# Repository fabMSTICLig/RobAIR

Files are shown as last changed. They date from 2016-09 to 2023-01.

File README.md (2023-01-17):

<br />Les différentes partie de ce projet sont mise à disposition selon les termes de la <a rel="license" href="http://creativecommons.org/licenses/by-nc-sa/3.0/fr/">Licence Creative Commons Attribution - Pas d’Utilisation Commerciale - Partage dans les Mêmes Conditions 3.0 France</a>.

---

Avec le soutien financier de la région Auvergne-Rhône-Alpes

---

# RobAIR

## Installation

### Pré-requis

- Ubuntu 20.04 LTS
- Git

- L'utilisateur courant doit avoir les droits root via `sudo`

### Procédure

- Téléchargez le dépôt
```bash
git clone https://github.com/FabmsticLig/RobAIR.git
```
- Lancez le script d'installation
```bash
cd RobAIR
./scripts/install.bash
```
- Si l'utilisateur courant n'était préalablement pas dans le groupe `dialout`
(autrement dit, si le script d'installation a affiché "donne à l'utilisateur
l'accès aux ports série"), redémarrez votre session
- Avec la carte Arduino branchée, lancez le chargement des programmes
```bash
robair reload
```

Le script d'installation récupérera des dépôts les paquets nécessaires et
effectuera la configuration initiale de RobAIR. Quelques variables seront aussi
ajoutées au bashrc de l'utilisateur, en plus d'un service systemd permettant de
démarrer et arrêter les programmes.

## Utilisation

### Procédure

Sur RobAIR
- Allumez le robot
- Allumez la tablette
- Branchez la tablette
- Connectez vous au réseau wifi. Si votre RobAIR dispose d'une carte wifi
externe pensez à déconnecter la carte wifi interne (INTEL).
- Ouvrez un terminal et lancez la commande `robair ip`, notez l'adresse IP indiquée (ROBAIR_IP)
- Lancez la commande `robair start`
- Ouvrez chromium et allez à l'adresse https://ROBAIR_IP:6080 (en remplaçant
ROBAIR_IP par l'adresse notée précédemment)

Sur la machine utilisateur
- Allez à l'adresse http://ROBAIR_IP:6081
- Récupérez l'autorité de certification et installez-la sur le navigateur client
- Allez à l'adresse https://ROBAIR_IP:6080

### Gestion

La partie logicielle de RobAIR peut être contrôlée depuis la tablette via le
programme `robair`. Utilisez les commandes suivantes pour respectivement lancer,
arrêter ou redémarrer le logiciel.
```bash
robair start
robair stop
robair restart
```

Si `systemd` est installé (par défaut sous Ubuntu), ces commandes pilotent
RobAIR via un service systemd en session utilisateur. L'intérêt est
essentiellement de permettre le lancement de RobAIR au démarrage, puis de gérer
automatiquement les erreurs (`systemd` relancera le logiciel s'il venait à
planter). Avec quelques modifications il serait aussi possible de
configurer l'activation par socket.

Le programme `robair` permet aussi la mise à jour du logiciel via cette commande
```bash
$ robair update
```
Cela récupérera la dernière version de RobAIR via Git, recompilera les
programmes et mettra à jour la carte Arduino.

## Développement

RobAIR est développé au-dessus de l'architecture [ROS][1].

L'essentiel du code du robot se trouve dans `arduino/libraries`, avec le point
d'entrée dans `arduino/robairarduino`.

L'interface est servie par un serveur `nodejs` résidant dans `interface`.

Si vous souhaitez tester des modifications locales, vous pouvez recompiler les
programmes et recharger la carte Arduino via cette commande
```bash
robair reload
```

 [1]: http://www.ros.org/

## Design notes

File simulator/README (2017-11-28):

                                   Robairsim

================================================================================

Ce programme simule un RobAIR avec sa carte Arduino (ou plus exactement son
processeur) et ses différents périphériques. Il récupère et interprète le
binaire robairarduino, qui doit être préalablement compilé. Cela permet le test
et le déboguage sans disposer de robot RobAIR opérationnel.

I/ Compilation
--------------

Récupérez la bonne version de simavr via le sous-module du dépôt :
$ git submodule update --init

Installez les paquets Debian / Ubuntu suivants :
 - freeglut3-dev
 - libelf-dev
 - libsdl2-dev
 - libsdl2-gfx-dev

Compilez robairsim :
$ make

Afin de faire fonctionner la liaison série virtuelle connectant le simulateur à
l'architecture ROS, vous aurez besoin de modifier le module rosserial.

Ouvrez ce fichier :
catkin_ws/src/rosserial/rosserial_python/src/rosserial_python/SerialClient.py

Vers la ligne 344, vous devriez trouver le code suivant :
                self.port = Serial(port, baud, timeout=self.timeout*0.5)

Modifiez cette ligne ainsi :
                self.port = Serial(port, baud, timeout=self.timeout*0.5, rtscts=True, dsrdtr=True)

Recompilez ensuite les modules ROS. Dans le répertoire catkin_ws :
$ catkin_make install

II/ Utilisation de base
-----------------------

Assurez-vous d'abord que le programme Arduino a été recompilé depuis les
dernières modifications. Pour le compiler, depuis le répertoire
arduino/robairarduino, lancez :
$ make

Depuis le répertoire simulator, lancez ensuite robairsim :
$ ./launch
Une fenêtre devrait apparaître, affichant l'état actuel du robot.

Lancez ou relancez ensuite ROS, dans un autre terminal :
$ robair restart

Patientez quelques instants que le processeur virtuel se réinitialise et que le
programme de la ros_lib publie les informations sur les topics émis et écoutés.
Tout devrait ensuite fonctionner comme sur un véritable RobAIR.

III/ Déboguage
--------------

Pour déboguer le programme de RobAIR via le simulateur, quelques étapes
supplémentaires sont nécessaires.

Vous aurez besoin du paquet Debian / Ubuntu nommé gdb-avr.

Tout d'abord, robairarduino doit être compilé avec les informations de débug.
Dans un fichier arduino/robairarduino/paths.mk, ajoutez les lignes suivantes :
---------8<--------
DEBUG = 1
OPTIMIZATION_LEVEL = 0 -gdwarf-4
--------->8--------

Puis recompilez le programme, dans arduino/robairarduino :
$ make clean
$ make

Lancez le simulateur en mode déboguage, dans simulator/ :
$ ./launch -g

Le simulateur va attendre une connexion gdb. Dans un autre terminal, lancez :
$ avr-gdb ../arduino/robairarduino/build-*/robairarduino.elf
> source gdbinit

Vous pourrez alors utiliser gdb normalement.

================================================================================

IV/ Fonctionnement interne
--------------------------

Robairsim est basé sur simavr, configuré pour simuler une Atmega2560. Il s'agit
du processeur de l'Arduino Mega.

Les périphériques sont émulés à bas niveau grâce au système d'irq de simavr, qui
permet de placer des hooks lors de l'écriture de certains registres,
l'expiration de timers, etc.

Le programme crée au démarrage une liaison série virtuelle sous le nom
/tmp/simavr-uart0. Si aucune carte Arduino n'est connectée lors du démarrage de
ROS (avec robair start) et que ce fichier existe, il est utilisé pour la
connexion avec rosserial.

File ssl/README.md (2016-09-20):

# SSL/TLS

Dans ce dossier doit se trouver les fichiers
device.crt  device.csr  device.key  rootCA.key  rootCA.crt  rootCA.srl
Mais ils ne doivent cependant pas apparaitre dans le dépot.

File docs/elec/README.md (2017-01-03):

#Fichiers mécaniques

Le fichier global.xml s'ouvre avec l'utilitaire umlet ou la version en ligne umletino.

##Kicad

Les schémas électroniques sont conçus avec le logiciel open source Kicad.

| Fichiers/dossiers | Explication |
|---|---|
| robair.lib | librairie kicad des composants du projet |
| robair.pretty | librairie d'empreinte kicad des composants du projet | 
| alim5v | le projet de la carte d'alimnetation | 
| cartehaute | le projet de la carte de connexion placé dans le buste  |

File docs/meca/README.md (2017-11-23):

# Fichiers mécaniques

Les fichiers svg contiennent les pièces à découper au laser. Ils ont été édités avec InkScape. Ils ne sont pas utilisable en l'état afin de pouvoir les modifier. La plupart des pièces nécéssitent la manipulation suivante :
* Sélectionner toute la pièce
* Menu->Objet->Dégrouper
* Menu->Edition->Cloner->Délier le clone
* Selectionner les éléments bleus si présents puis Menu->Chemin->Union
* Sélectionner tous les éléments de la pièce sauf ceux avec un contour vert ou fond gris
* Menu->Chemin->Exclusion
* Mettre ensuite les paramètres pour votre découpeuse (Exemple : pas de fond, Contour : Couleur (R:255 G:0 B:0), Epaisseur:0.01in )

Les fichiers terminant par LC sont prêts à être découpé pour des planches de 400x600mm.

Les fichiers scad sont les fichiers sources OpenScad et les fichiers stl les fichiers correspondant à imprimer en 3D.

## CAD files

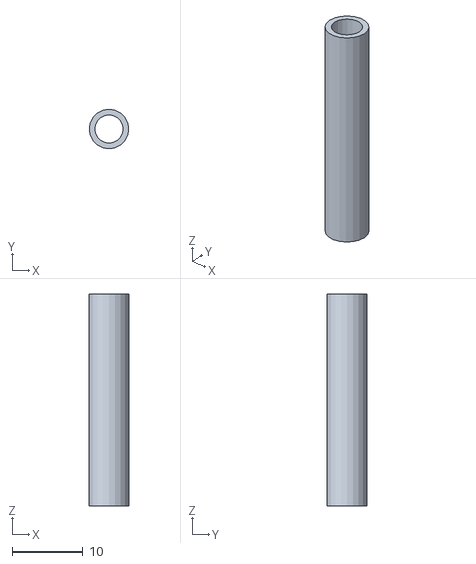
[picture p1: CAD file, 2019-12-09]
docs/meca/callecarte30.stl
5.60 x 5.60 x 30.0

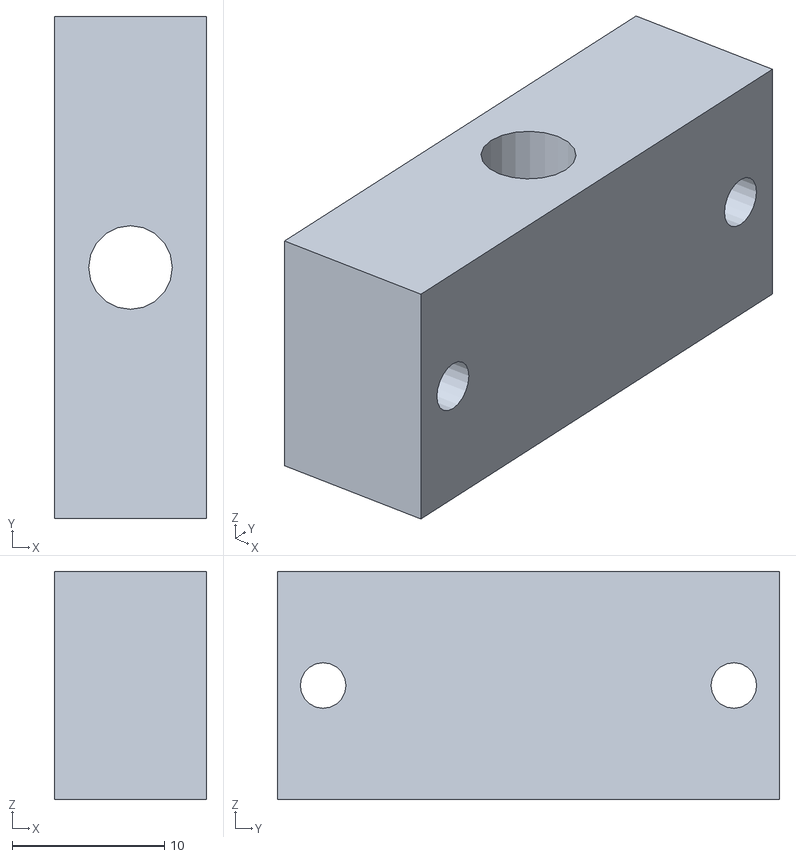
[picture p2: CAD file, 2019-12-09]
docs/meca/voltholder.stl
10.0 x 33.0 x 15.0

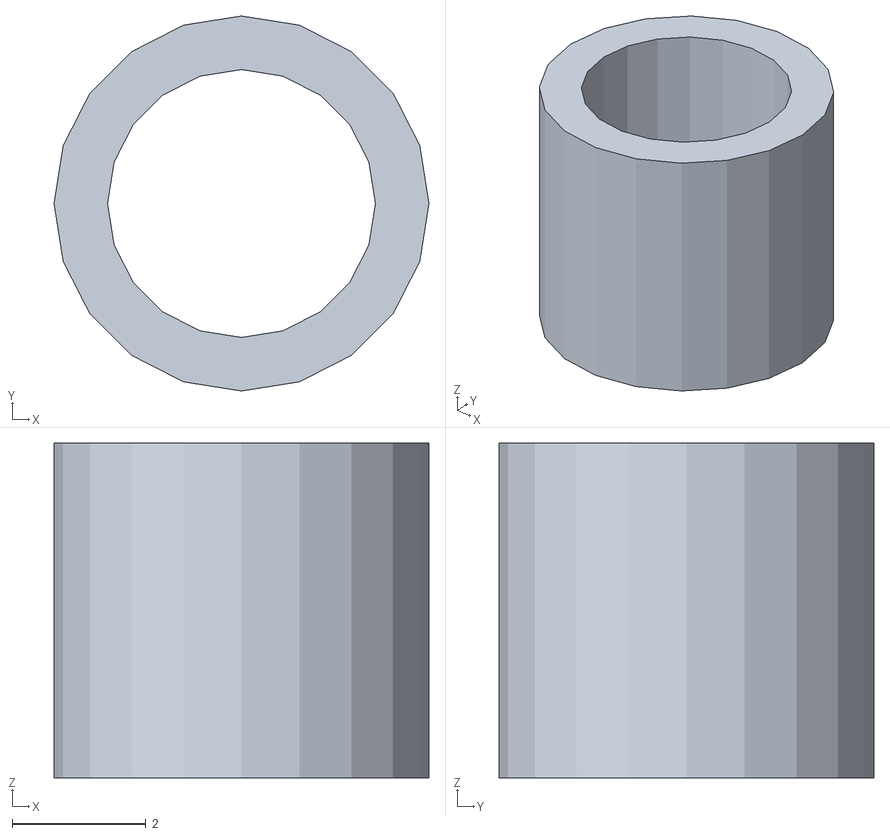
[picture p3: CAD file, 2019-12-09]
docs/meca/callecarte5.stl
5.60 x 5.60 x 5.00

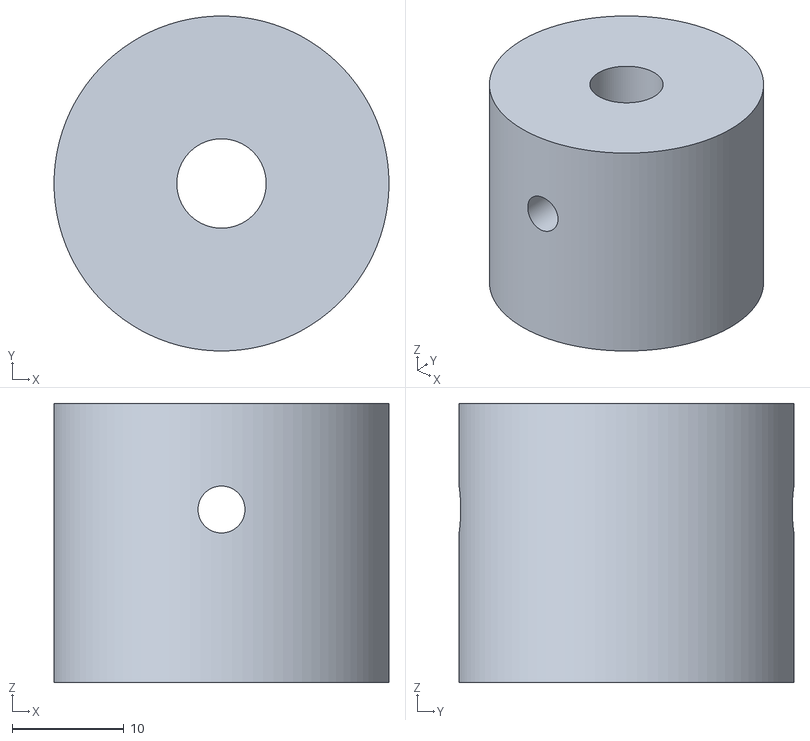
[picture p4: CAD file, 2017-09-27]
docs/meca/goupilleservo.stl
30.0 x 30.0 x 25.0

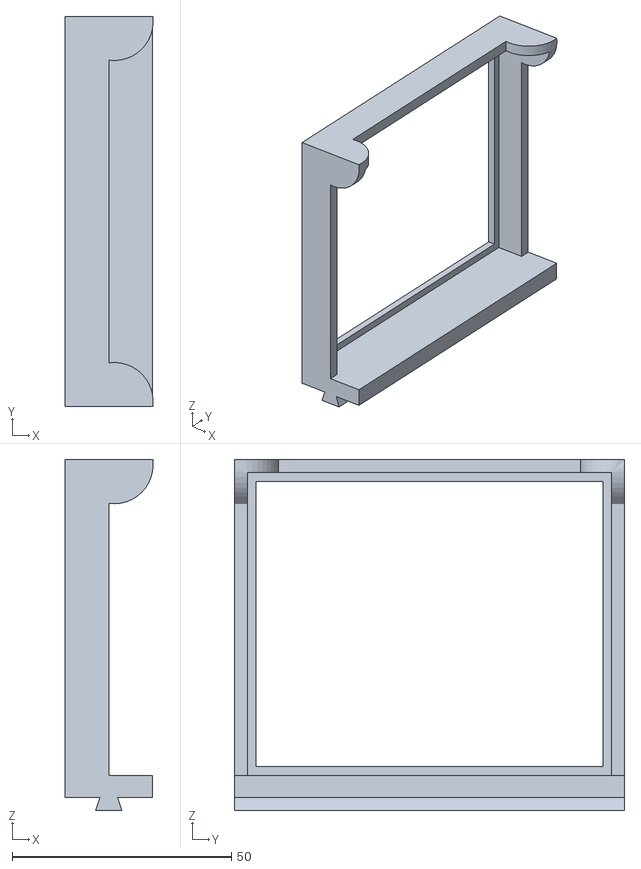
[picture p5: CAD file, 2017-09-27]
docs/meca/JBL_box.stl
20.1 x 89.0 x 80.0

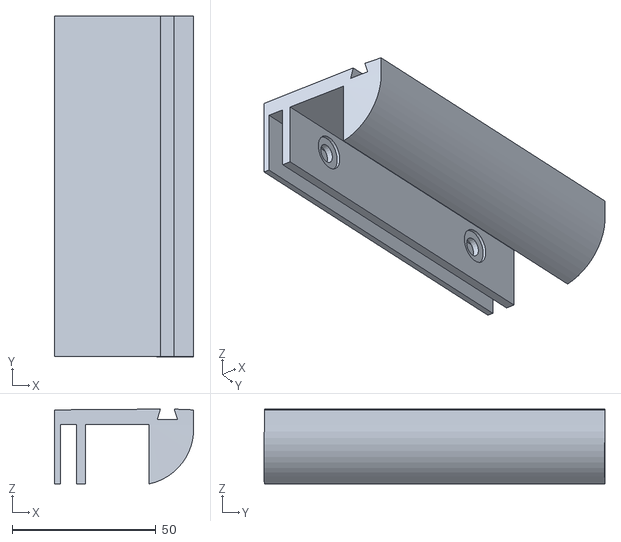
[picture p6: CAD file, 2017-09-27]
docs/meca/holdertablet_base.stl
48.5 x 118.6 x 26.0

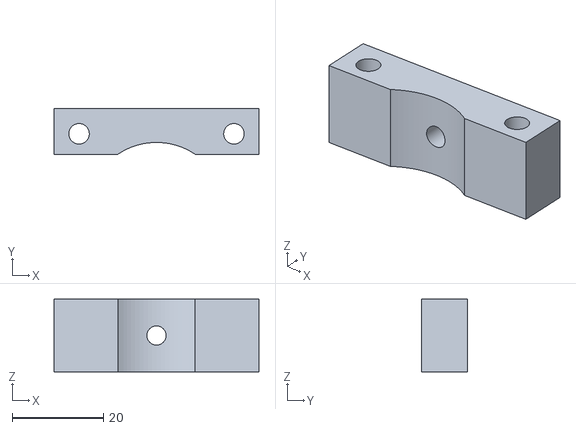
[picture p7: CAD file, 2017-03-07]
docs/meca/goupilletete.stl
45.0 x 10.0 x 16.0

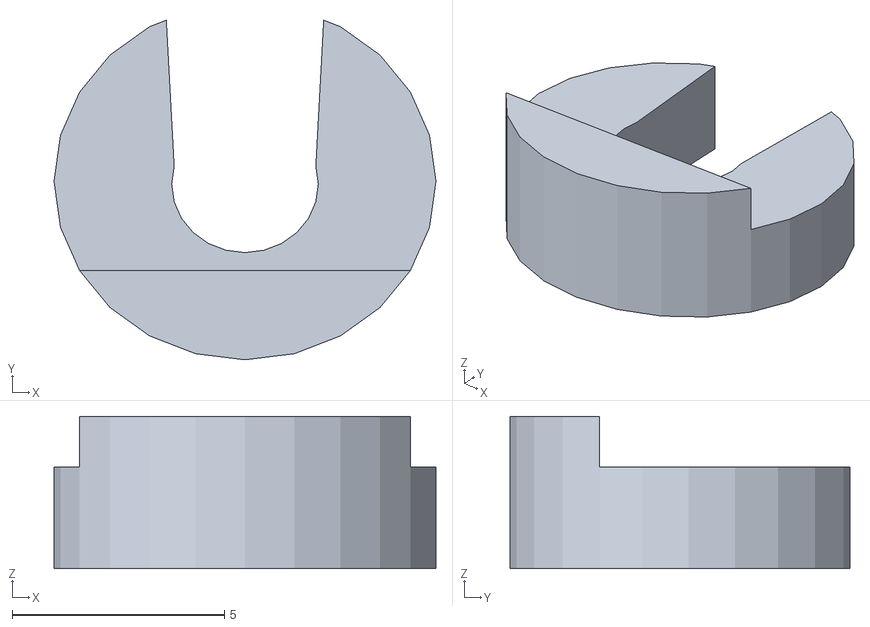
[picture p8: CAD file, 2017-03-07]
docs/meca/clips4mm.stl
9.00 x 8.00 x 3.59

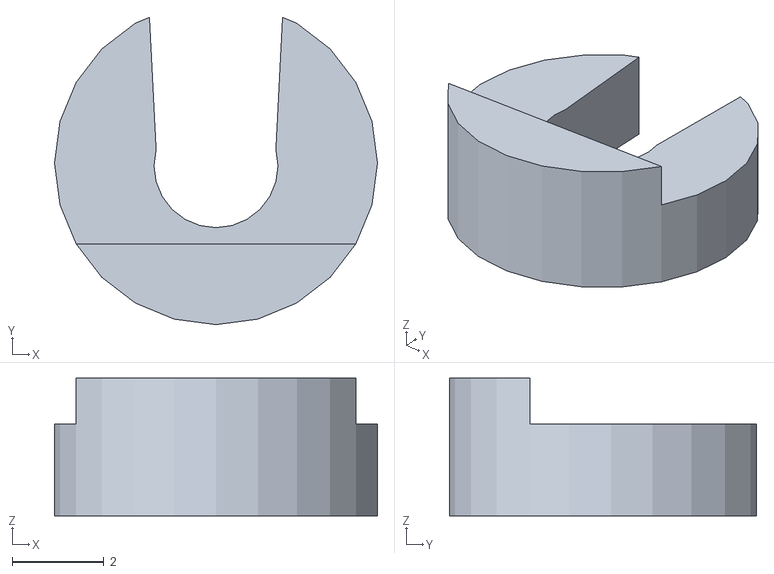
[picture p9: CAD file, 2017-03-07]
docs/meca/clips3mm.stl
7.03 x 6.69 x 3.00

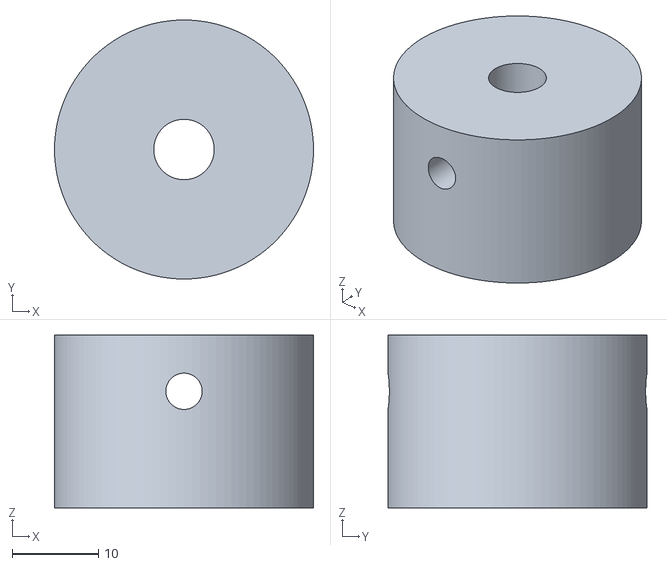
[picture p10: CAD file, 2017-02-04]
docs/meca/goupilleservomini.stl
30.0 x 30.0 x 20.0

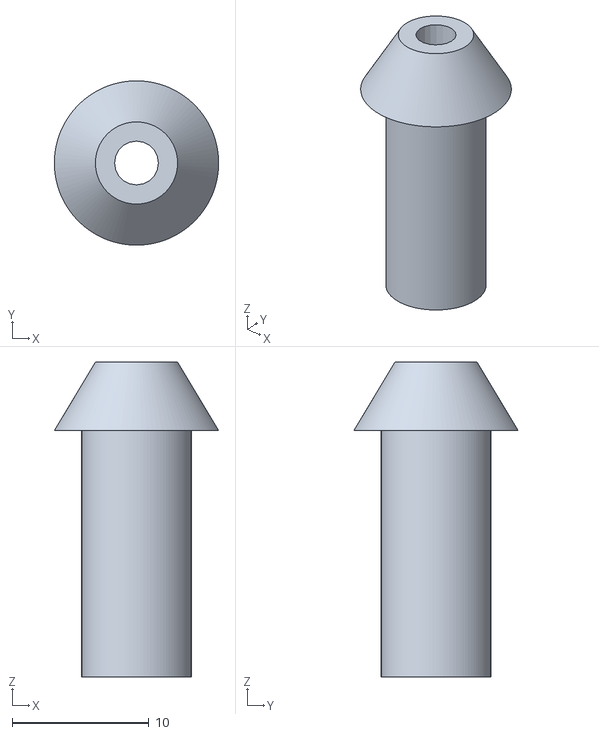
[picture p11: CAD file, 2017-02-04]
docs/meca/holdertablet_arm.stl
12.0 x 12.0 x 23.0

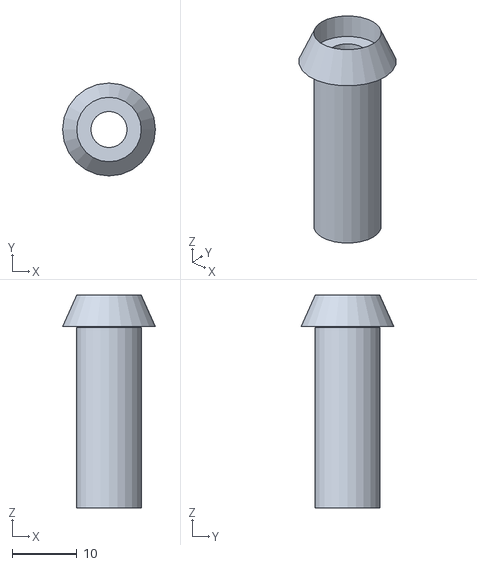
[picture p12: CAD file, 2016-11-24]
docs/meca/coin_tablette_hoder.stl
14.4 x 14.4 x 33.0

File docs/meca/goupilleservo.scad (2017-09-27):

difference()
{
    cylinder (h = 25, r=15, center = true, $fn=100);
    cylinder (h = 25, r=4, center = true, $fn=100);
    translate ([0,0,4.5])rotate([90,0,0]) cylinder (h = 100, r=2.1, center = true, $fn=100);
    
    translate ([8,0,-5])cylinder (h = 10, r=0.5, center = true, $fn=10);
    translate ([-8,0,-5])cylinder (h = 10, r=0.5, center = true, $fn=10);
    translate ([0,7,-5])cylinder (h = 10, r=0.5, center = true, $fn=10);
    translate ([0,-7,-5])cylinder (h = 10, r=0.5, center = true, $fn=10);
}

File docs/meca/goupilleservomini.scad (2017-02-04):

difference()
{
    cylinder (h = 20, r=15, center = true, $fn=100);
    cylinder (h = 20, r=3.5, center = true, $fn=100);
    translate ([0,0,3.5])rotate([90,0,0]) cylinder (h = 100, r=2.1, center = true, $fn=100);
    
    translate ([10,0,-5])cylinder (h = 10, r=0.75, center = true, $fn=10);
    rotate([0,0,90])translate ([10,0,-5])cylinder (h = 10, r=0.75, center = true, $fn=10);
    rotate([0,0,180])translate ([10,0,-5])cylinder (h = 10, r=0.75, center = true, $fn=10);
    rotate([0,0,270])translate ([10,0,-5])cylinder (h = 10, r=0.75, center = true, $fn=10);
}

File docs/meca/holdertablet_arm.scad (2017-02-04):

difference(){
    
    union(){
        cylinder (h = 19, r=4, center = false, $fn=100);
        translate([0,0,18])cylinder (h = 5, r1=6, r2=3, center = false, $fn=100);
    }
    cylinder (h = 23, r=1.6, center = false, $fn=20);
}

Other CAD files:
docs/meca/servomount.stl
docs/meca/callecarte30.scad
docs/meca/JBL_box.skp
docs/meca/callecarte5.scad
docs/meca/goupilletete.scad
docs/meca/holdertablet_base.skp
docs/meca/voltholder.scad

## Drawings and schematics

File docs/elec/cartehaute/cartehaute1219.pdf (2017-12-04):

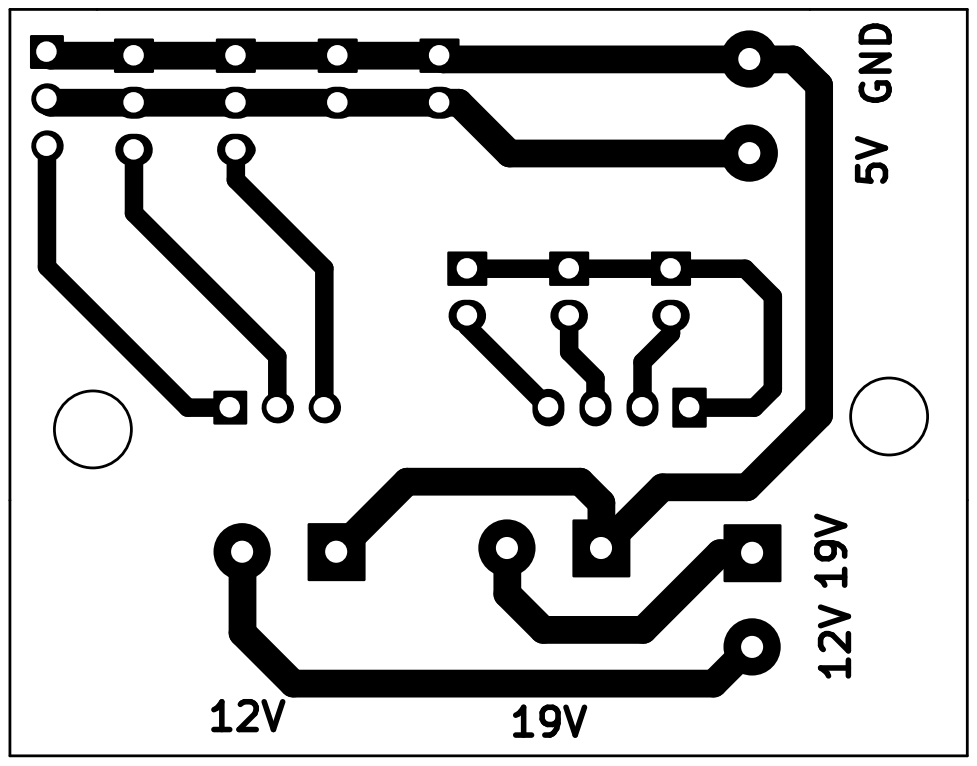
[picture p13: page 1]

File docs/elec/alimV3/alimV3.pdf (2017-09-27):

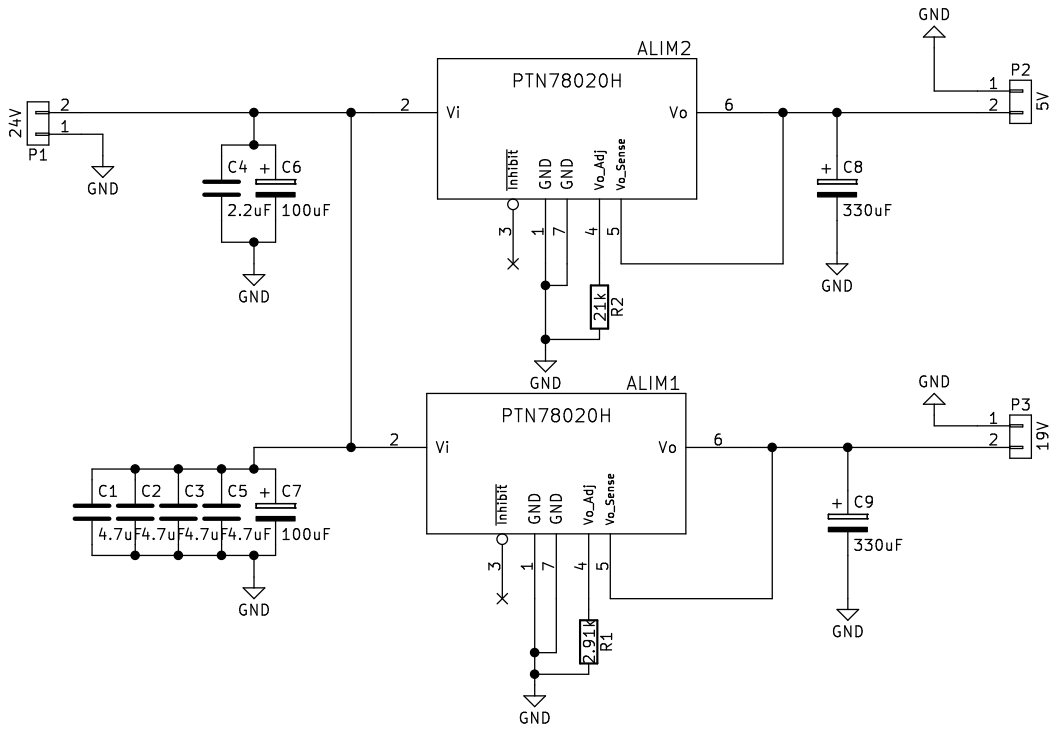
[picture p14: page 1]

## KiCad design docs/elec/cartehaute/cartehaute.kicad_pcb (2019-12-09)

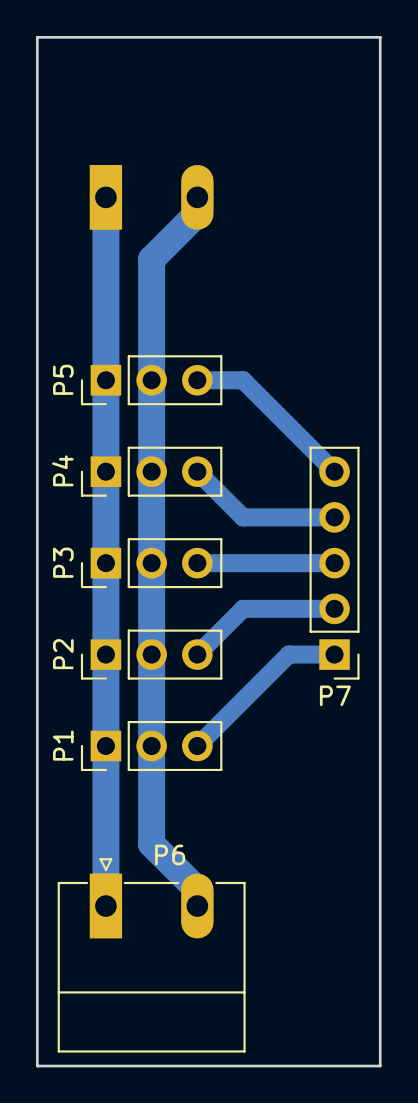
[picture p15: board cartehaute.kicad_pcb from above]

Board: 2 copper layers, 19.1 x 57.2 mm, 8 parts (1 on the bottom side), 7 nets.

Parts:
P1: D1; Pin_Header_Straight_1x03_Pitch2.54mm
P2: D2; Pin_Header_Straight_1x03_Pitch2.54mm
P3: D3; Pin_Header_Straight_1x03_Pitch2.54mm
P4: D4; Pin_Header_Straight_1x03_Pitch2.54mm
P5: D5; Pin_Header_Straight_1x03_Pitch2.54mm
P6, P8: CONN_01X02; PhoenixContact_MC-G_02x5.08mm_Angled
P7: CONN_01X05; Pin_Header_Straight_1x05_Pitch2.54mm

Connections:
/5V: P1.2, P2.2, P3.2, P4.2, P5.2, P6.2, P8.2
/GND: P1.1, P2.1, P3.1, P4.1, P5.1, P6.1, P8.1
unnamed: P1.3, P7.1
unnamed: P2.3, P7.2
unnamed: P3.3, P7.3
unnamed: P4.3, P7.4
unnamed: P5.3, P7.5

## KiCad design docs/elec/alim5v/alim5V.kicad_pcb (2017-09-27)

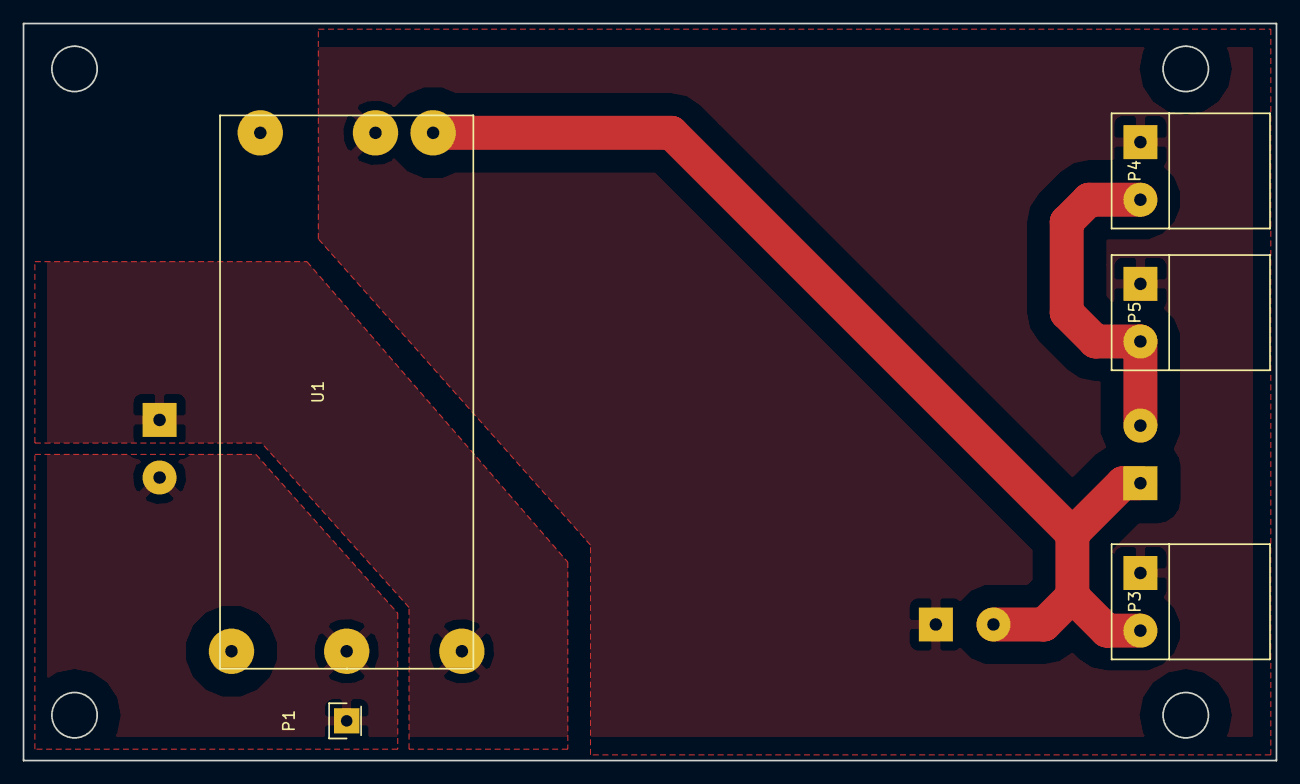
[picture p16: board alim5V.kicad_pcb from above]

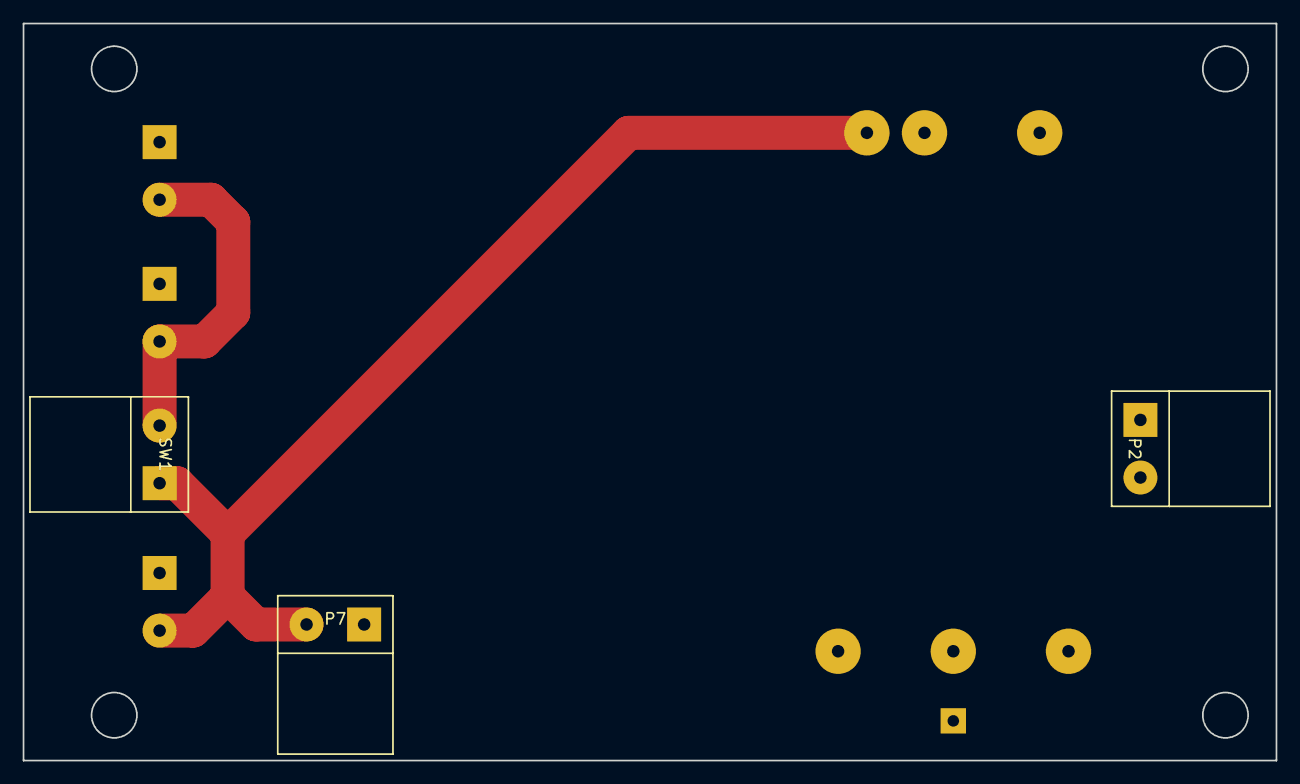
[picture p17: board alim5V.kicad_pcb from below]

Board: 2 copper layers, 110.5 x 65.0 mm, 8 parts (3 on the bottom side), 5 nets.

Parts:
P1: GND Ardui; Pin_Header_Straight_1x01
P2: 5V out; Bornier5mm
P3: MD49; Bornier5mm
P4: Charg; Bornier5mm
P5: Batt; Bornier5mm
P7: AUX; Bornier5mm
SW1: SW; Bornier5mm
U1: UEI30-050-Q12P-C

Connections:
/GND5: P1.1, P2.2, U1.5
/GND24: P3.1, P4.1, P5.1, P7.1, U1.2
unnamed: P2.1, U1.4
unnamed: P3.2, P7.2, SW1.1, U1.1
unnamed: P4.2, P5.2, SW1.2

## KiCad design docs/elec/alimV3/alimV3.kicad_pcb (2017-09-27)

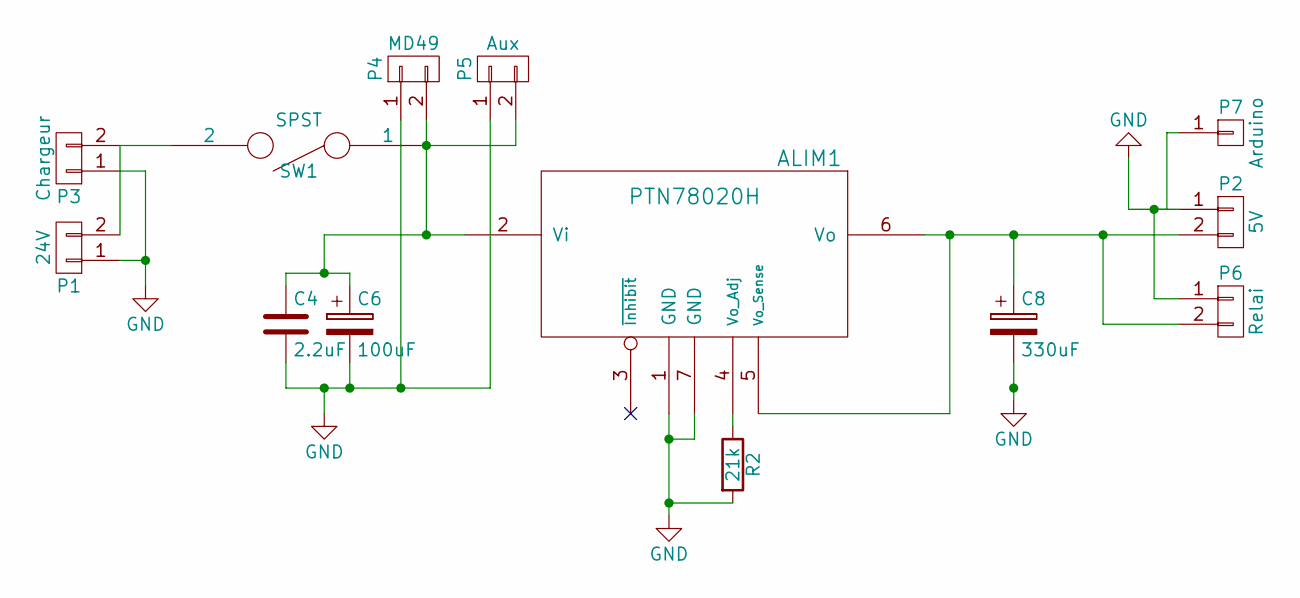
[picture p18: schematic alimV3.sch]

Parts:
ALIM1: PTN78020H; PTN78020
C4: 2.2uF; C_1210_HandSoldering
C6: 100uF; CP_Radial_D6.3mm_P2.50mm
C8: 330uF; CP_Radial_D10.0mm_P5.00mm
P1: 24V; Bornier5mm
P2: 5V; Bornier5mm
P3: Chargeur; Bornier5mm
P4: MD49; Bornier5mm
P5: Aux; Bornier5mm
P6: Relai; Socket_Strip_Straight_2x01_Pitch2.54mm
P7: Arduino; Socket_Strip_Straight_1x01_Pitch2.54mm
R2: 21k; R_Axial_DIN0204_L3.6mm_D1.6mm_P2.54mm_Vertical
SW1: SPST; Bornier5mm

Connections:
GND: ALIM1.1 (GND), ALIM1.7 (GND), C4.2, C6.2, C8.2, P1.1, P2.1, P3.1, P4.1, P5.1, P6.1, P7.1, R2.2; also elsewhere on the board
unnamed 1: ALIM1.2 (Vi), C4.1, C6.1, P4.2, P5.2, SW1.1; also elsewhere on the board
unnamed 3: ALIM1.4 (Vo_Adj), R2.1; also elsewhere on the board
unnamed 4: ALIM1.5 (Vo_Sense), ALIM1.6 (Vo), C8.1, P2.2, P6.2; also elsewhere on the board
unnamed: P1.2, P3.2, SW1.2

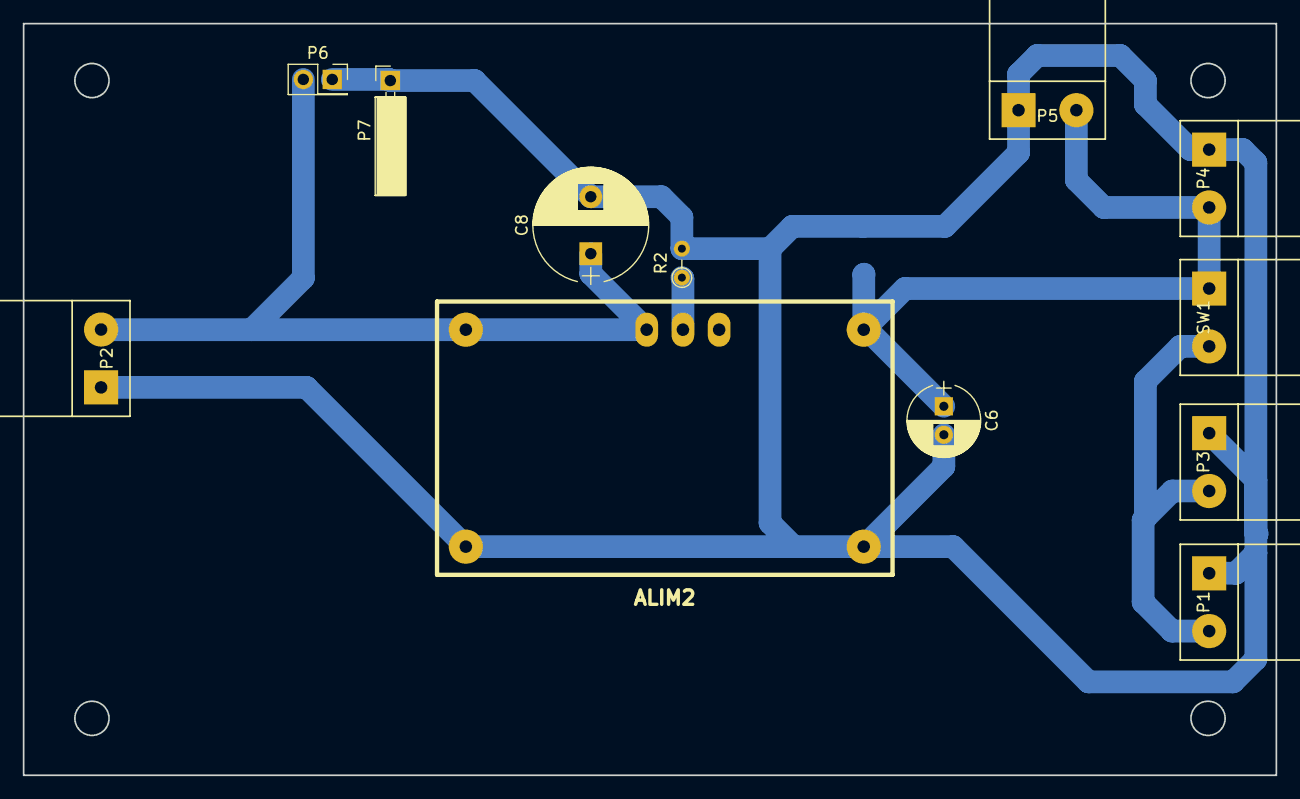
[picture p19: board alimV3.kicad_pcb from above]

Board: 2 copper layers, 110.0 x 66.0 mm, 13 parts (1 on the bottom side), 5 nets.

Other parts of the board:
ALIM2: PTN78020H; PTN78020

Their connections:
GND: ALIM2.1, ALIM2.7; also elsewhere on the board
unnamed 1: ALIM2.2; also elsewhere on the board
unnamed 3: ALIM2.4; also elsewhere on the board
unnamed 4: ALIM2.5, ALIM2.6; also elsewhere on the board

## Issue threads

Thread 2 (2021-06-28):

sks-keyservers ceased operations - install script broken

vincent38, 2021-06-28:
Hello,

The install script is relying on the hkp://ha.pool.sks-keyservers.net:80 keyserver at the ros repository addition step, which is no longer maintained as of 2021-06-21 (see https://sks-keyservers.net/status/).

https://github.com/fabMSTICLig/RobAIR/blob/41760ffbf5440ad7c021b45cf6684af9f87fb061/scripts/install.bash#L155

The output log is the following:
```
Ajout de l'utilisateur « root » au groupe « dialout »...
Ajout de l'utilisateur root au groupe dialout
Fait.
Executing: /tmp/tmp.oVzrFevTGI/gpg.1.sh --keyserver
hkp://ha.pool.sks-keyservers.net:80
--recv-key
0xB01FA116
gpg: demande de la clef B01FA116 sur le serveur hkp ha.pool.sks-keyservers.net
?: ha.pool.sks-keyservers.net: Host not found
gpgkeys: HTTP fetch error 7: couldn't connect: Connection refused
gpg: aucune donnée OpenPGP valable n'a été trouvée.
gpg: Quantité totale traitée : 0
gpg: erreur de communication avec le serveur de clefs : keyserver unreachable
gpg: erreur de communication avec le serveur de clefs : clef publique introuvable
gpg: échec de réception depuis le serveur de clefs : clef publique introuvable
```

It might be a good idea to switch to a different keyserver.

Regards

Pikrass, 2021-07-06:
Additionally, we shouldn't use apt-key anymore, it's deprecated. The new way of adding third party repositories is detailed [there](https://wiki.debian.org/DebianRepository/UseThirdParty).

In short: create a /usr/local/share/keyrings directory if it doesn't exist, download the key there with `gpg`, and add its path to a "signed-by" attribute in the sources.list.d file.

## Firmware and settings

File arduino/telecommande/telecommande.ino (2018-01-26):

#include <math.h>

#define PIN_X A1
#define PIN_Y A0

int rest_dx, rest_dy;

void setup()
{
	Serial.begin(9600);

	rest_dx = 512 - analogRead(PIN_X);
	rest_dy = 512 - analogRead(PIN_Y);
}

void analogGamepad(float dx, float dy, float *linear, float *angular)
{
	float norm = sqrt(dx * dx + dy * dy);

	if (norm < 0.01) {
		*linear = 0.0;
		*angular = 0.0;
		return;
	}

	if (norm > 1) {
		dx = dx / norm;
		dy = dy / norm;
		norm = 1;
	}

	float theta = atan(dy / dx);
	if (dx < 0)
		theta = theta + PI;
	else if (dy < 0)
		theta = theta + 2 * PI;

	*linear = sin(theta) * norm;
	*angular = -1. * cos(theta) * norm * 0.5 / 0.2;
}

void loop()
{
	float dx = map(analogRead(PIN_X) + rest_dx, 0, 1023, -100, 100) / 100.0,
	       dy = map(analogRead(PIN_Y) + rest_dy, 0, 1023, -100, 100) / 100.0;

	union { uint8_t i[4]; float f; } linear, angular;

	analogGamepad(dx, dy, &linear.f, &angular.f);

	Serial.write("\xff\xff\xff\xff");
	Serial.write(linear.i, 4);
	Serial.write(angular.i, 4);
	delay(100);
}

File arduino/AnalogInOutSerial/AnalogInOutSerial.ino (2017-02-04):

/*
  Analog input, analog output, serial output
 
 Reads an analog input pin, maps the result to a range from 0 to 255
 and uses the result to set the pulsewidth modulation (PWM) of an output pin.
 Also prints the results to the serial monitor.
 
 The circuit:
 * potentiometer connected to analog pin 0.
   Center pin of the potentiometer goes to the analog pin.
   side pins of the potentiometer go to +5V and ground
 * LED connected from digital pin 9 to ground
 
 created 29 Dec. 2008
 modified 9 Apr 2012
 by Tom Igoe
 
 This example code is in the public domain.
 
 */

// These constants won't change.  They're used to give names
// to the pins used:
const int an0 = A0;  // Analog input pin that the potentiometer is attached to
const int an2 = A1;
const int an4 = A2;  // Analog input pin that the potentiometer is attached to
const int an5 = A3;

int sensorValue = 0;        // value read from the pot
int sensorF = 0;        // value read from the pot
int sensorR = 0;        // value read from the pot
int outputValue = 0;        // value output to the PWM (analog out)

void setup() {
  // initialize serial communications at 9600 bps:
  Serial.begin(9600); 
  sensorF = analogRead(A0);
  sensorR = analogRead(A1);
  sensorF = analogRead(A2);
  sensorR = analogRead(A3);
}

void loop() {
  // read the analog in value:
  sensorValue = analogRead(A0);    
  Serial.print("A0 = " );                       
  Serial.println(sensorValue);   
  
  sensorValue = analogRead(A1);    
  Serial.print("A1 = " );                       
  Serial.println(sensorValue);      
  sensorValue = analogRead(A2);    
  Serial.print("A2 = " );                       
  Serial.println(sensorValue);      
  sensorValue = analogRead(A3);    
  Serial.print("A3 = " );                       
  Serial.println(sensorValue);                   
  Serial.println();                        
  Serial.println();      

  // wait 2 milliseconds before the next loop
  // for the analog-to-digital converter to settle
  // after the last reading:
  delay(400);                     
}

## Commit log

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2016-10-28 kicad project
    [robair.kicad_pcb, robair.sch]
2016-11-12 fix install.bash
    option -e enlevée, l'option non compatible avec `cat ~/.bashrc | grep ROBAIR`, supposément l'utilisation des ``
2016-11-19 reboot interface robair, preparation changement arduino vers lib Robair
2016-11-20 elec : alim haut, alim bas. mecas
    [base_tablette_hoder.stl, cartehaute.kicad_pcb, cartehaute.sch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]
2016-11-24 ros ajout de rosparam dans ros arduino, gestion des bumper (en cours), gestion de l'aru
2016-11-27 correction de la résoltion de ROBAIR_IP en cas de connection offline
2016-11-27 correction de l'affichage des yeux
2016-11-28 ajout script de démarage correction de la gestion des yeux bumper ok touch ok
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2016-11-29 gestion de la fermeture de la fenetre de controle
2016-12-01 netoyage des fichiers meca, création de la base de charge
    [cartehaute.kicad_pcb]
2016-12-01 Maj Readme
    Ajout section Utilisation
    + Suite explication des Scripts
2016-12-06 correction de script
2016-12-06 ajout carte alim 5V
    [alim5V.kicad_pcb, alim5V.sch]
2016-12-08 Ajout de l'option pour mettre à jour RoAIR
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2016-12-10 changement de install.sh pour passer à arduino 1.6.5, amélioration script changeip
2016-12-25 ajout fichiers decoupes laser
    [goupilleservomini.scad, goupilleservomini.stl]
2016-12-25 ajout connecteur carte puissance
    [alim5V.kicad_pcb, alim5V.sch]
2017-01-03 ajout svg elec et suppression V1
    [cartehaute.kicad_pcb, cartehaute.sch, robair.kicad_pcb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]
2017-01-05 ajout changement de la matrice des yeux par ros
2017-01-16 sortie de robair.launch du git, ajout d'un fichier par défaut
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2017-01-16 ajout d'un script permettant de modifier les fichiers de configurations selon le ROBAIR_HOME, sortie des fichiers impactés du git et ajout des fichiers par defaut
2017-01-25 robair script: transfert du changement d'ip et d'arduino dans le script robair
2017-02-04 mise a jour base avec sangle modification goopillette hauteur trou ajout d'un fichier model des bras retenant la tablette
    [goupilleservomini.scad, goupilleservomini.stl, holderarm.scad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]
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2017-03-07 maj meca
    [clips3mm.stl, clips4mm.stl, goupilleservo.scad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]
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2017-03-21 Corrige la gestion du timeout dans MD49::getInt
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2017-03-21 Lance le noeud d'odométrie avec ses paramètres en même temps que robair
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2017-03-21 Lance le noeud urg_node au démarrage de RobAir pour le capteur Lidar
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2017-03-23 Gère le mouvement de la tête de RobAIR avec le stick de droite
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2017-03-23 Corrige l'orientation des yeux à gauche et à droite
2017-03-23 Corrige l'arc de cercle indiquant la position actuelle de la tête
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2017-03-29 Corrige le nom des frames pour les transforms envoyées
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2017-03-30 Place robair.launch dans son répertoire
    Etant donné que plus aucun script ne modifie robair.launch, on se
    débarrasse du mécanisme de copie. Cela nous permet en particulier de
    mettre à jour le fichier via Git.
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2017-03-31 Utilise des chemins relatifs pour la configuration du serveur interface
    Cela nous permet de nous débarasser du script changehome.sh, et en règle
    générale de toute dépendance au répertoire d'installation
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2017-04-14 Utilise la bibliothèque Adafruit_TiCoServo pour piloter la tête
    Contrairement à la bibiliothèque Servo, celle-ci n'utilise pas
    d'interruptions pour piloter les servomoteurs. A la place, elle tire
    profit des timers 16 bits du microcontrolleur, capables de générer
    automatiquement des impulsions avec la bonne largeur (PWM).
    Cela permet d'utiliser les NeoPixels sans déranger le contrôle du
    servomoteur. En effet, la configuration des LEDs se fait par l'envoi
    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
2017-05-18 Ajoute l'adresse IP en altname pour le certificat x509
    Ceci est requis par Chrome depuis la version 58. Les certificats x509 v1
    avec uniquement un CN (Common Name) ne sont plus supportés. Ce commit
    permet de générer des certificats x509 v3 avec un SAN (Subject
    Alternative Name).
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2017-06-28 Détecte la carte Arduino dans `robair reload` pour la passer au Makefile
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2017-06-28 Exclut du dépôt les fichiers de back-up de différents éditeurs de texte
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2017-06-28 Corrige le redémarrage de RobAIR lors d'un update ou d'un reload
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2017-06-28 Corrige l'affichage quand les scripts sont lancés sans terminal
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2017-06-28 Corrige le problème d'accès à la carte Arduino au démarrage
    Ce problème était causé par ModemManager qui utilisait le port série de
    l'Arduino pour tester s'il s'agissait d'un modem. Cela est réglé en
    attachant une propriété au périphérique lors de son traitement par udev.
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2017-06-28 Ne lisse pas le changement de vitesse si la commande est cmdvel
2017-07-17 Ajoute un support pour l'enceinte en-dessous de la tablette
    [JBL_box.stl, base_tablette_hoder.stl, base_tablette_holder.stl]
2017-09-27 update meca file
    [JBL_box.skp, base_tablette_hoder.skp, goupilleservo.scad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]
2017-09-27 update elec
    [alim5V.kicad_pcb, alimV3.kicad_pcb, alimV3.sch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]
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2017-10-16 Utilise le faux port série de l'émulateur si aucun Arduino n'est branché
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2017-10-16 Effectue un make clean sur le code Arduino lors d'un robair reload
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2017-10-19 Arrête le robot quand il ne reçoit plus de cmd_vel pour un certain temps
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2017-10-20 Ajoute une mailmap pour uniformiser le retour de git shortlog
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2017-10-27 Corrige la vitesse angulaire demandée par l'interface
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2017-10-27 Corrige l'envoi périodique des messages cmd_vel
2017-10-27 Corrige l'ordre des moteurs pour les commandes SET_SPEED du MD49
2017-11-02 Corrige le coding style et un nom de variable dans la partie interface
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2017-11-02 Implémente la correction de la distortion de la vidéo du robot
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2017-11-02 Enregistre les préférences vis-à-vis de la correction de la vidéo
2017-11-02 Récupère les paramètres de la correction fisheye au chargement
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2017-11-03 Corrige une faute de frappe dans le code Arduino
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2017-11-28 fix la dependence de odometry au messages robairmain
2017-11-28 [robairsim] Corrige le flag de debug dans le README pour utiliser DWARF4
2017-11-28 Lance `git submodule sync` lors d'un robair update
    Cette commande permet de mettre à jour les liens vers les dépôts
    distants des sous-modules en fonction du contenu de .gitmodules.
    Cela signifie que si l'on souhaite utiliser un autre fork d'un
    sous-module (par exemple le nôtre, avec nos propres modifications), il
    n'y aura qu'à corriger .gitmodules et ce changement sera répercuté dans
    les dépôts eux-mêmes lors du lancement de robair reload. Sans cette
    commande, git serait incapable de récupérer les commits souhaités pour
    les sous-modules qui ont changé de dépôt.
2017-11-28 Corrige les noms du package et des noeuds pour l'odométrie
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2017-12-04 Ajoute les connecteurs 12 et 19V sur la carte haute
    [cartehaute.kicad_pcb, cartehaute.sch]
2017-12-05 ajout carte alimentation générique
    [alim5V.kicad_pcb, alim5V.sch]
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2017-12-13 Utilise la dernière carte Arduino même si non branchée
    Avec la nouvelle version de rosserial_python, cela permet de démarrer
    ROS sans la carte, et de l'initialiser dès qu'elle sera effectivement
    branchée. Il n'est donc plus nécessaire de redémarrer le logiciel après
    avoir branché le hub USB à la tablette.
2018-01-10 Corrige la détermination de l'adresse locale pour le serveur web
2018-01-11 Corrige la commande pour obtenir l'IP de la machine
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2018-01-23 Corrige le noeud odometry
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2018-01-26 Corrige la mise en forme du code de la télécommande côté RobAIR
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2018-05-21 docs réajustement du pcb de la carte alim
    [alim5V.kicad_pcb]
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2018-07-21 Renommage des fichiers du porte tablette
    [holdertablet_arm.scad, holdertablet_arm.stl, holdertablet_base.skp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]
2018-12-03 Correction des evenements touch
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2019-01-17 correction des événements touch pour smartphone et tablette
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2019-06-19 Add hold file for the electronic tower
    [callecarte30.scad, callecarte5.scad]
2019-12-09 Simplify the top board
    [cartehaute.kicad_pcb, cartehaute.sch]
2019-12-09 Add the model of two hold for the electronical tower
    [callecarte30.stl, callecarte5.stl, voltholder.scad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]
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
